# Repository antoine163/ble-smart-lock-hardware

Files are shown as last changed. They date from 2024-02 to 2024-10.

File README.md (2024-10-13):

# Bluetooth LE Smart Lock - Hardware

## Cartes électronique
Ce dépôt contient deux cartes :
- **[BleSmartLock](BleSmartLock/README.md)**: La carte principale, construite autour du bluenrg-m2, inclut toute l'électronique de contrôle pour la serrure.
- **[LightSensor](LightSensor/README.md)**: Cette carte contient le capteur de lumière, permettant de le placer à distance. Cette carte est optionnelle.

## Réalisation

### Liste du matérielle:
Cette liste de matériel est disponible sur Amazon.
- [Alimentation 12V](https://www.amazon.fr/dp/B0924XBMCF?ref=ppx_yo2ov_dt_b_fed_asin_title&th=1) pour alimenter la serrure.
- [Serrure électromécanique](https://www.amazon.fr/dp/B07KWMH16C?ref=ppx_yo2ov_dt_b_fed_asin_title) pour la partie électromécanique de la serrure.
- [Bouton lumineux](https://www.amazon.fr/dp/B0CBRFQLLT?ref=ppx_yo2ov_dt_b_fed_asin_title&th=1) pour l'ouverture de la serrure et visualisation de l'état de la serrure.
- [Boîtier étanche](https://www.amazon.fr/dp/B09V7M8759?ref=ppx_yo2ov_dt_b_fed_asin_title) pour recevoir la carte électronique principale *BleSmartLock*.
- [Câble 4 conducteurs](https://www.amazon.fr/dp/B0BFWJ19YJ?ref=ppx_yo2ov_dt_b_fed_asin_title&th=1) pour la connexion entre la carte électronique principale et:
    - La serrure électromécanique
    - Le bouton lumineux
    - L'éclairage d'ambiance
    - Le capteur de lumière
    - L'éclairage extérieur
- [Câble 2 conducteurs](https://www.amazon.fr/dp/B0B7WV1QCW?ref=ppx_yo2ov_dt_b_fed_asin_title) pour l'alimentation.
- [Presse-étoupes](https://www.amazon.fr/dp/B07V7F5HKQ?ref=ppx_yo2ov_dt_b_fed_asin_title&th=1) pour faire passer les différents câbles dans les boîtiers étanches.
- [Boîtier étanche](https://www.amazon.fr/dp/B0BZCS1PN1?ref=ppx_yo2ov_dt_b_fed_asin_title) pour recevoir le capteur de luminosité *LightSensor* et la lampe extérieur *Mini-Light*.
- [Colle epoxy transparent](https://www.amazon.fr/dp/B07JL8JC3N?ref=ppx_yo2ov_dt_b_fed_asin_title) pour réaliser une vitre dans le boîtier du capteur de luminosité et de la lampe extérieur.

### Mise en boiter de la carte principal *BleSmartLock* 
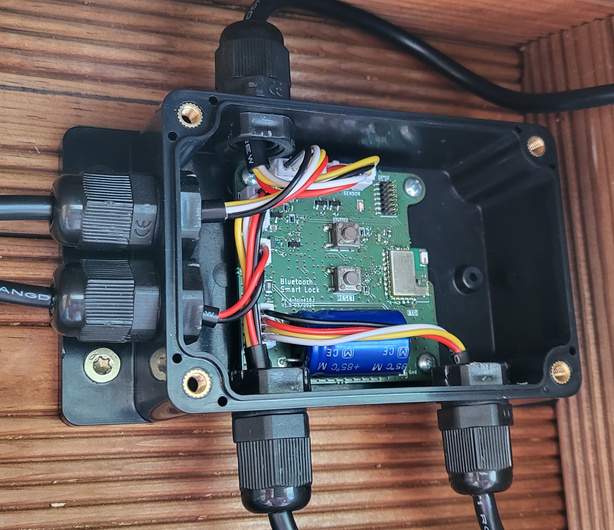
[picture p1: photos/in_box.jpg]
in box
  

### Mise en boiter de la carte capteur *LightSensor* et lampe extérieur *Mini-Light*
On notera ici que 2 cartes *Mini-Light* ont été utilisées pour augmenter la luminosité de la lampe extérieur.  
**NOTE:** Un maximum de 2 cartes *Mini-Light* peut être utilisé directement à la carte principale *BleSmartLock*.  
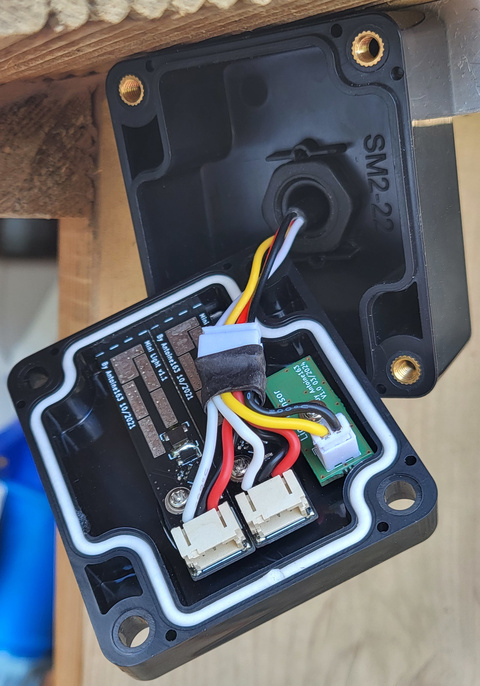
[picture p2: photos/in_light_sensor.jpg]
in light sensor


Au préalable, il est nécessaire de percer un trou rectangulaire et un trou rond dans le couvercle du boîtier, puis de les remplir de colle époxy transparente. Cela permet de créer des vitres, assurant ainsi le passage de la lumière utile au capteur de luminosité et d'éclairage extérieur.  
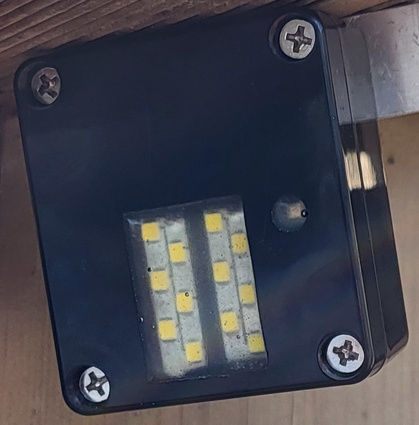
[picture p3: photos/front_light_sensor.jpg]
front light sensor


## Prototypes
### Avec les cartes v1.0
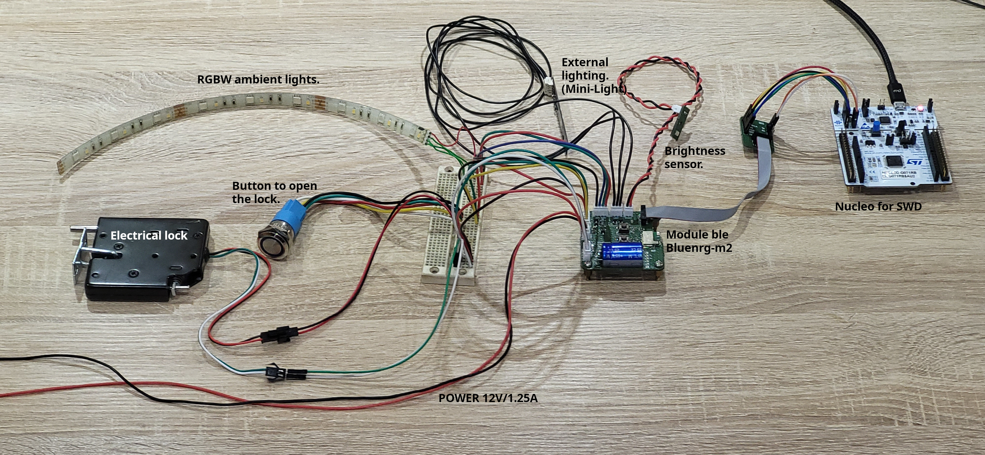
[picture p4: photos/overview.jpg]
Prototype cartes v1.0


### Sur plaque d'essai
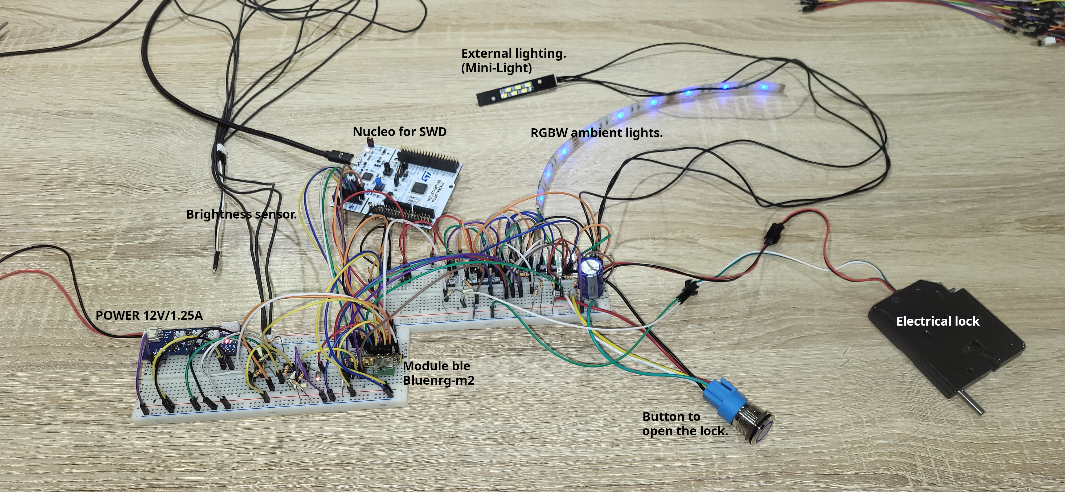
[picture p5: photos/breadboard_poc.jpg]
Prototype breadboard


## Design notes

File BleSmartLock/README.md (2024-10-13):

# BleSmartLock Board
Cette carte est la carte principale du projet. Elle est basée sur le module radio Bluenrg-m2 et fais l'interface avec les autres organes, telle que la serrure elle-même et le bouton pour l'ouverture.

Voir le [README](../../Firmware/README.md) du firmware pour la programmation de cette carte.

## Vue 3D
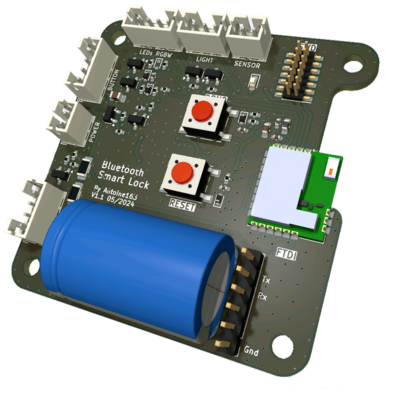
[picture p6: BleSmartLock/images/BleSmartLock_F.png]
BleSmartLock front
 
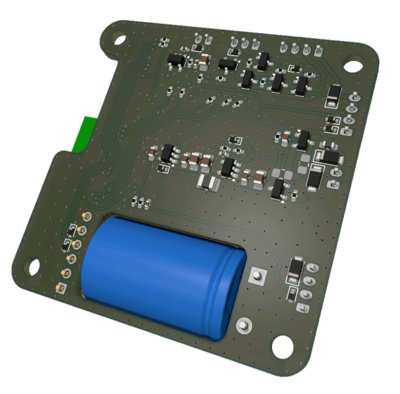
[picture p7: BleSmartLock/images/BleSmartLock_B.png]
BleSmartLock back
 

## Réalisation
### Fabrication de la version v1.0
#### Correction
Une erreur c'est glissée à la saisie de la schématique. DIO12 peut seulement être une entrée. la version v1.1 inverse DIO12 avec DIO6.
Il faut inverser c'est deux gpio sur le pcb en coupent deux pistes et en croisent les connections.
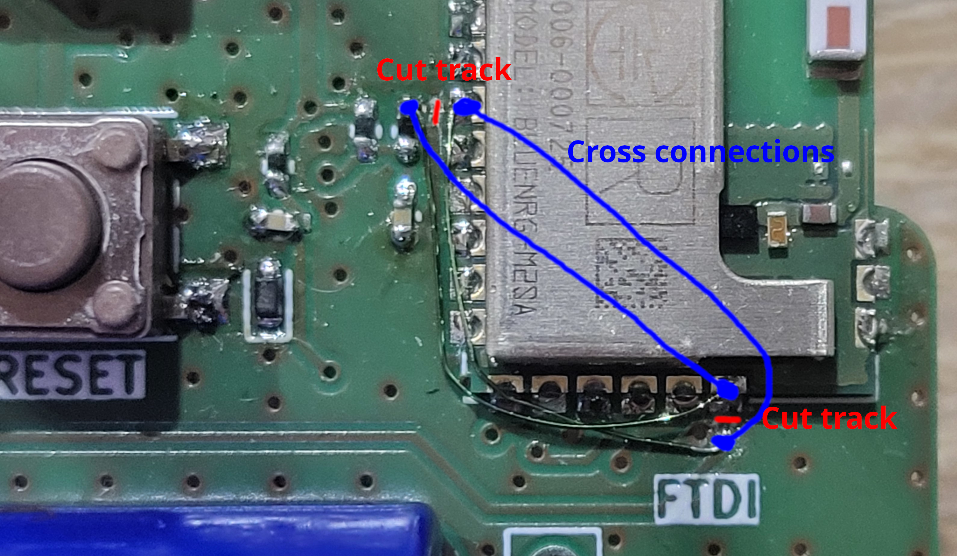
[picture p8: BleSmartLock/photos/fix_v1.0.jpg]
BleSmartLock fix v1.0


#### Photos
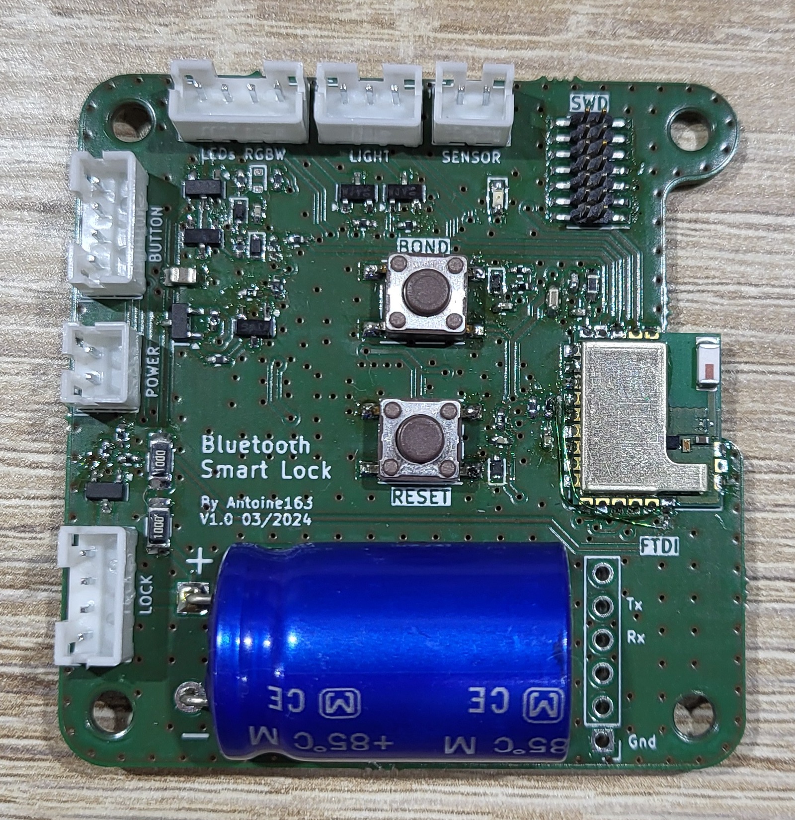
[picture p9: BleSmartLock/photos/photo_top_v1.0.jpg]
BleSmartLock photo top

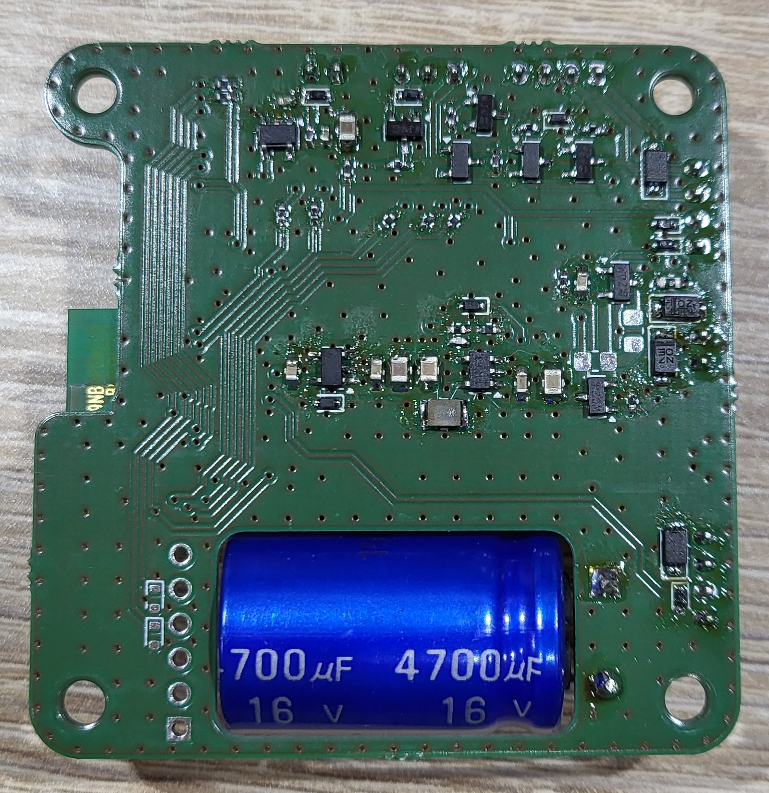
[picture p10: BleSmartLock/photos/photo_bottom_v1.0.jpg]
BleSmartLock photo top

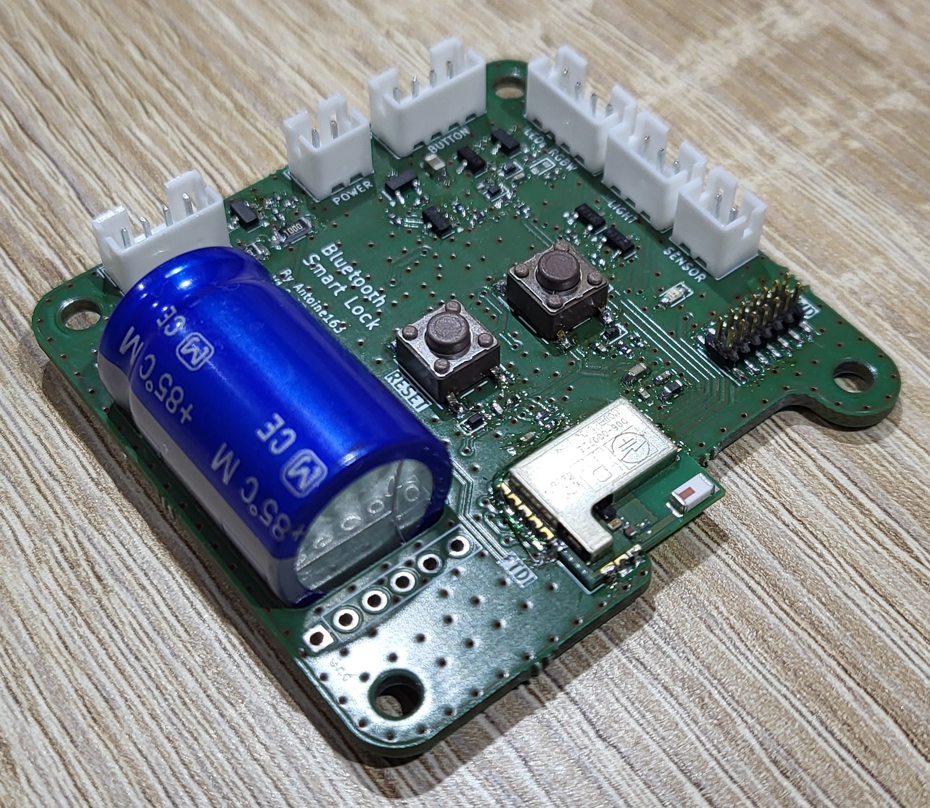
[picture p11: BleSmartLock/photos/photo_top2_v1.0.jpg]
BleSmartLock photo top

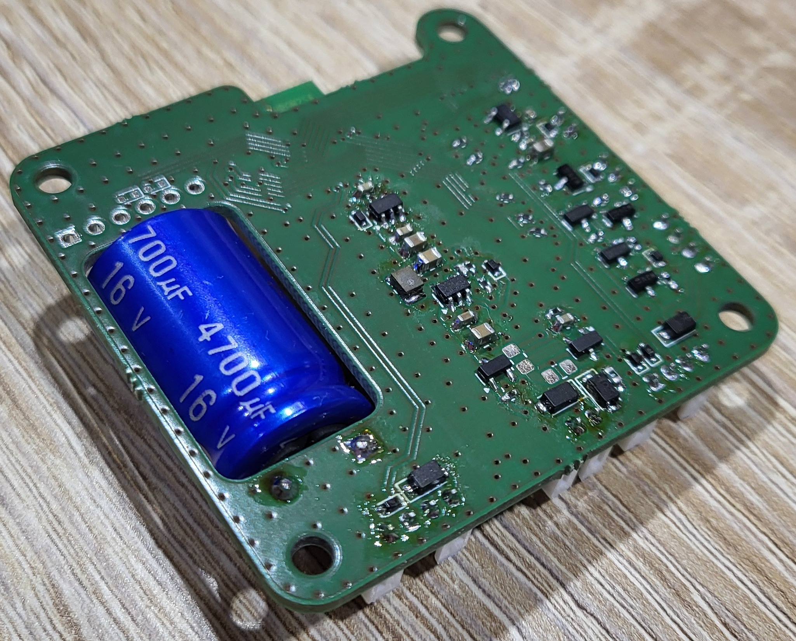
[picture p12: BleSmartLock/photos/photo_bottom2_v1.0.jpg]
BleSmartLock photo top


#### BOM
La bom interactive est trouvable [ici](https://antoine163.github.io/ble-smart-lock-hardware/Ble_Smart_Lock_1.0-ibom.html). 

### Fabrication de la version v1.1
Je n'est pas fabrique cette version, mais elle dispose exactement des mêmes composent que la v1.0.
La bom interactive est trouvable [ici](https://antoine163.github.io/ble-smart-lock-hardware/Ble%20Smart%20Lock-1.1-ibom.html). 

# Schématique





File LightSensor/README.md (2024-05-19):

# BleSmartLock-LightSensor Board
C'est la carte satellite permettant de déporter le capteur de luminosité. Elle est constituée principalement du capteur KPS-3227.

## Vue 3D
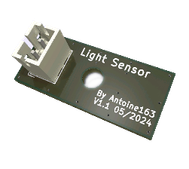
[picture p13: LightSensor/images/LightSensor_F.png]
LightSensor front
 
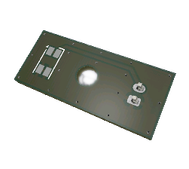
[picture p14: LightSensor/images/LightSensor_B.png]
LightSensor back
 

## Réalisation
### Fabrication de la version v1.0
#### Photos
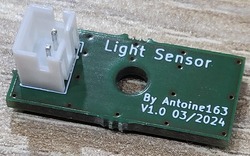
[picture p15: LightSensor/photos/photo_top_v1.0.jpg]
BleSmartLock photo top

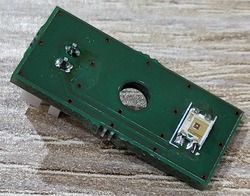
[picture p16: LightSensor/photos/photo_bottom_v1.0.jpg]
BleSmartLock photo bottom


#### BOM
Cette carte est constituée seulement d'un connecteur JST et du capteur de lumière ambiante:
- JST: [B2B-PH-K-S](https://www.amazon.fr/gp/product/B0731MZCGF/ref=ppx_yo_dt_b_asin_title_o02_s00?ie=UTF8&psc=1).
- KINGBRIGHT: [KPS-3227SP1C](https://fr.farnell.com/kingbright/kps-3227sp1c/capteur-optique-phototransistor/dp/2373478). 

### Fabrication de la version v1.1
Je n'est pas fabrique cette version, seulement le connecteur à été tournée de 180 degrés.

# Schématique


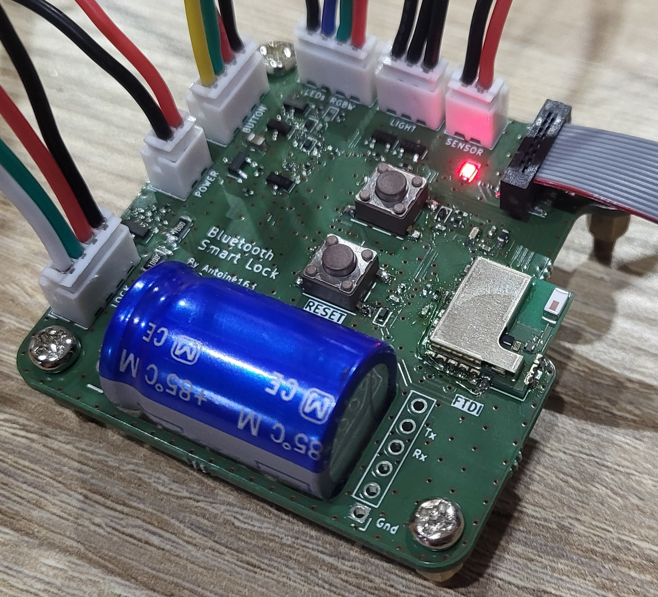
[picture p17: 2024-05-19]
BleSmartLock/photos/photo_top_v1.0back.jpg

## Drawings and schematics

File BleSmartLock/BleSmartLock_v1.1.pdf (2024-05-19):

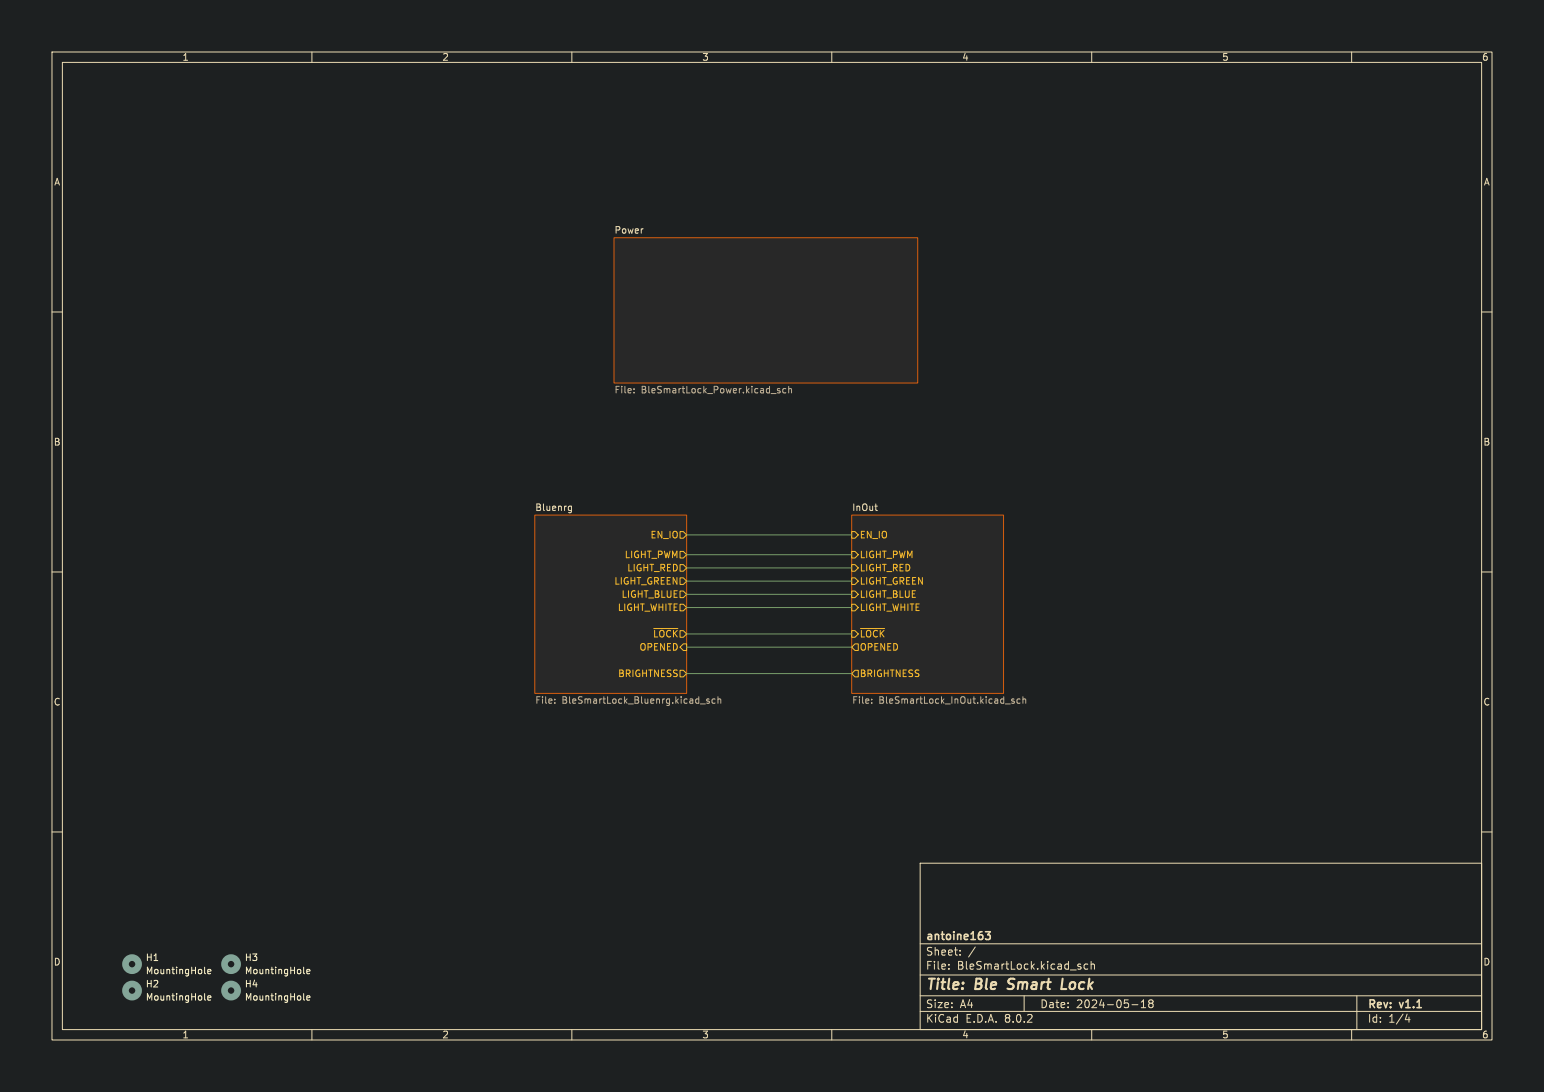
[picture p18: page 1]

Id: 1/4 Title: Ble Smart Lock

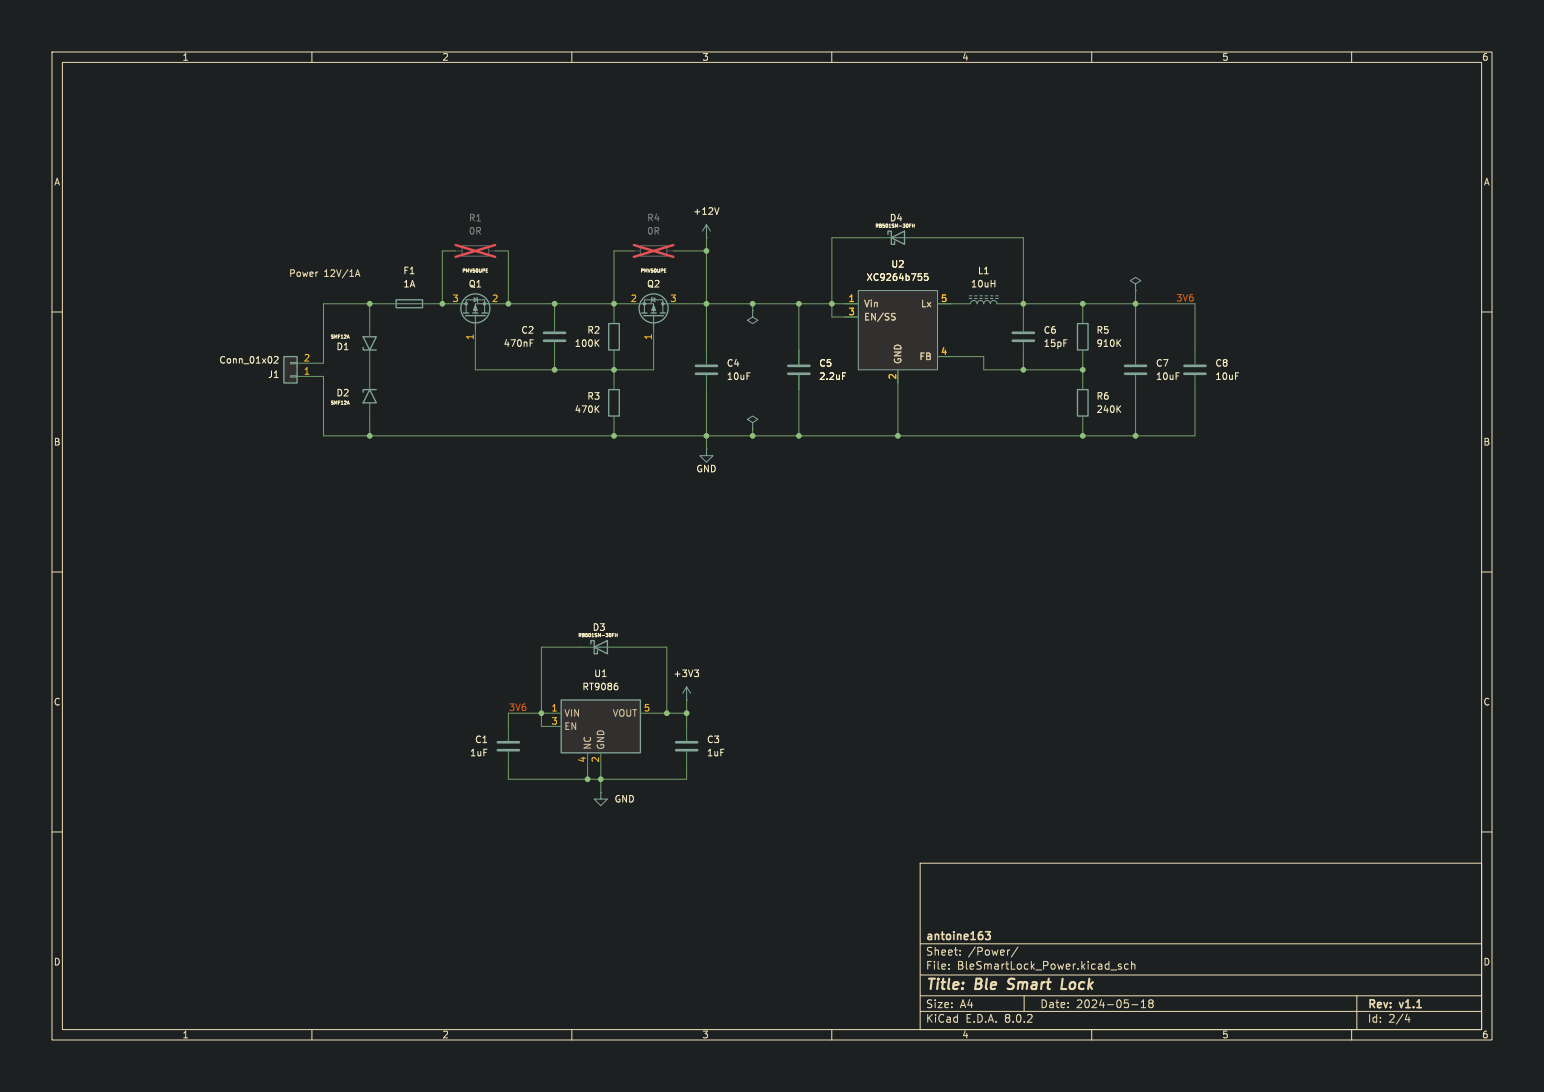
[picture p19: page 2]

Id: 2/4 Title: Ble Smart Lock

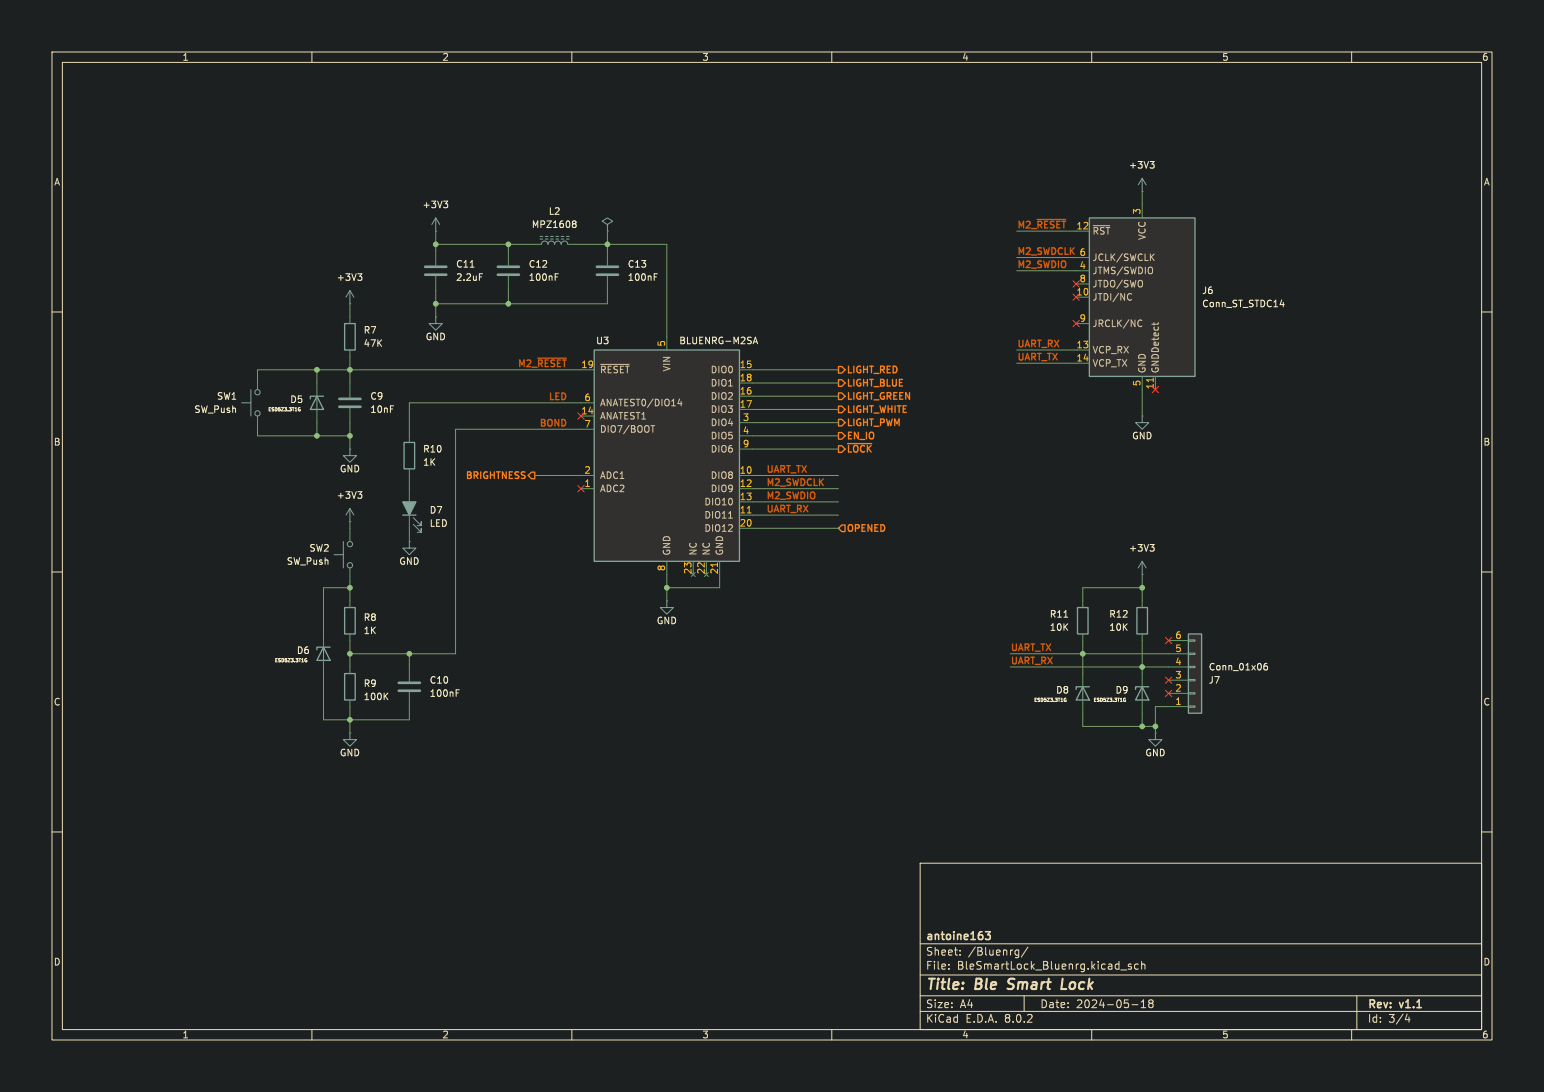
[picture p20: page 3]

Id: 3/4 Title: Ble Smart Lock

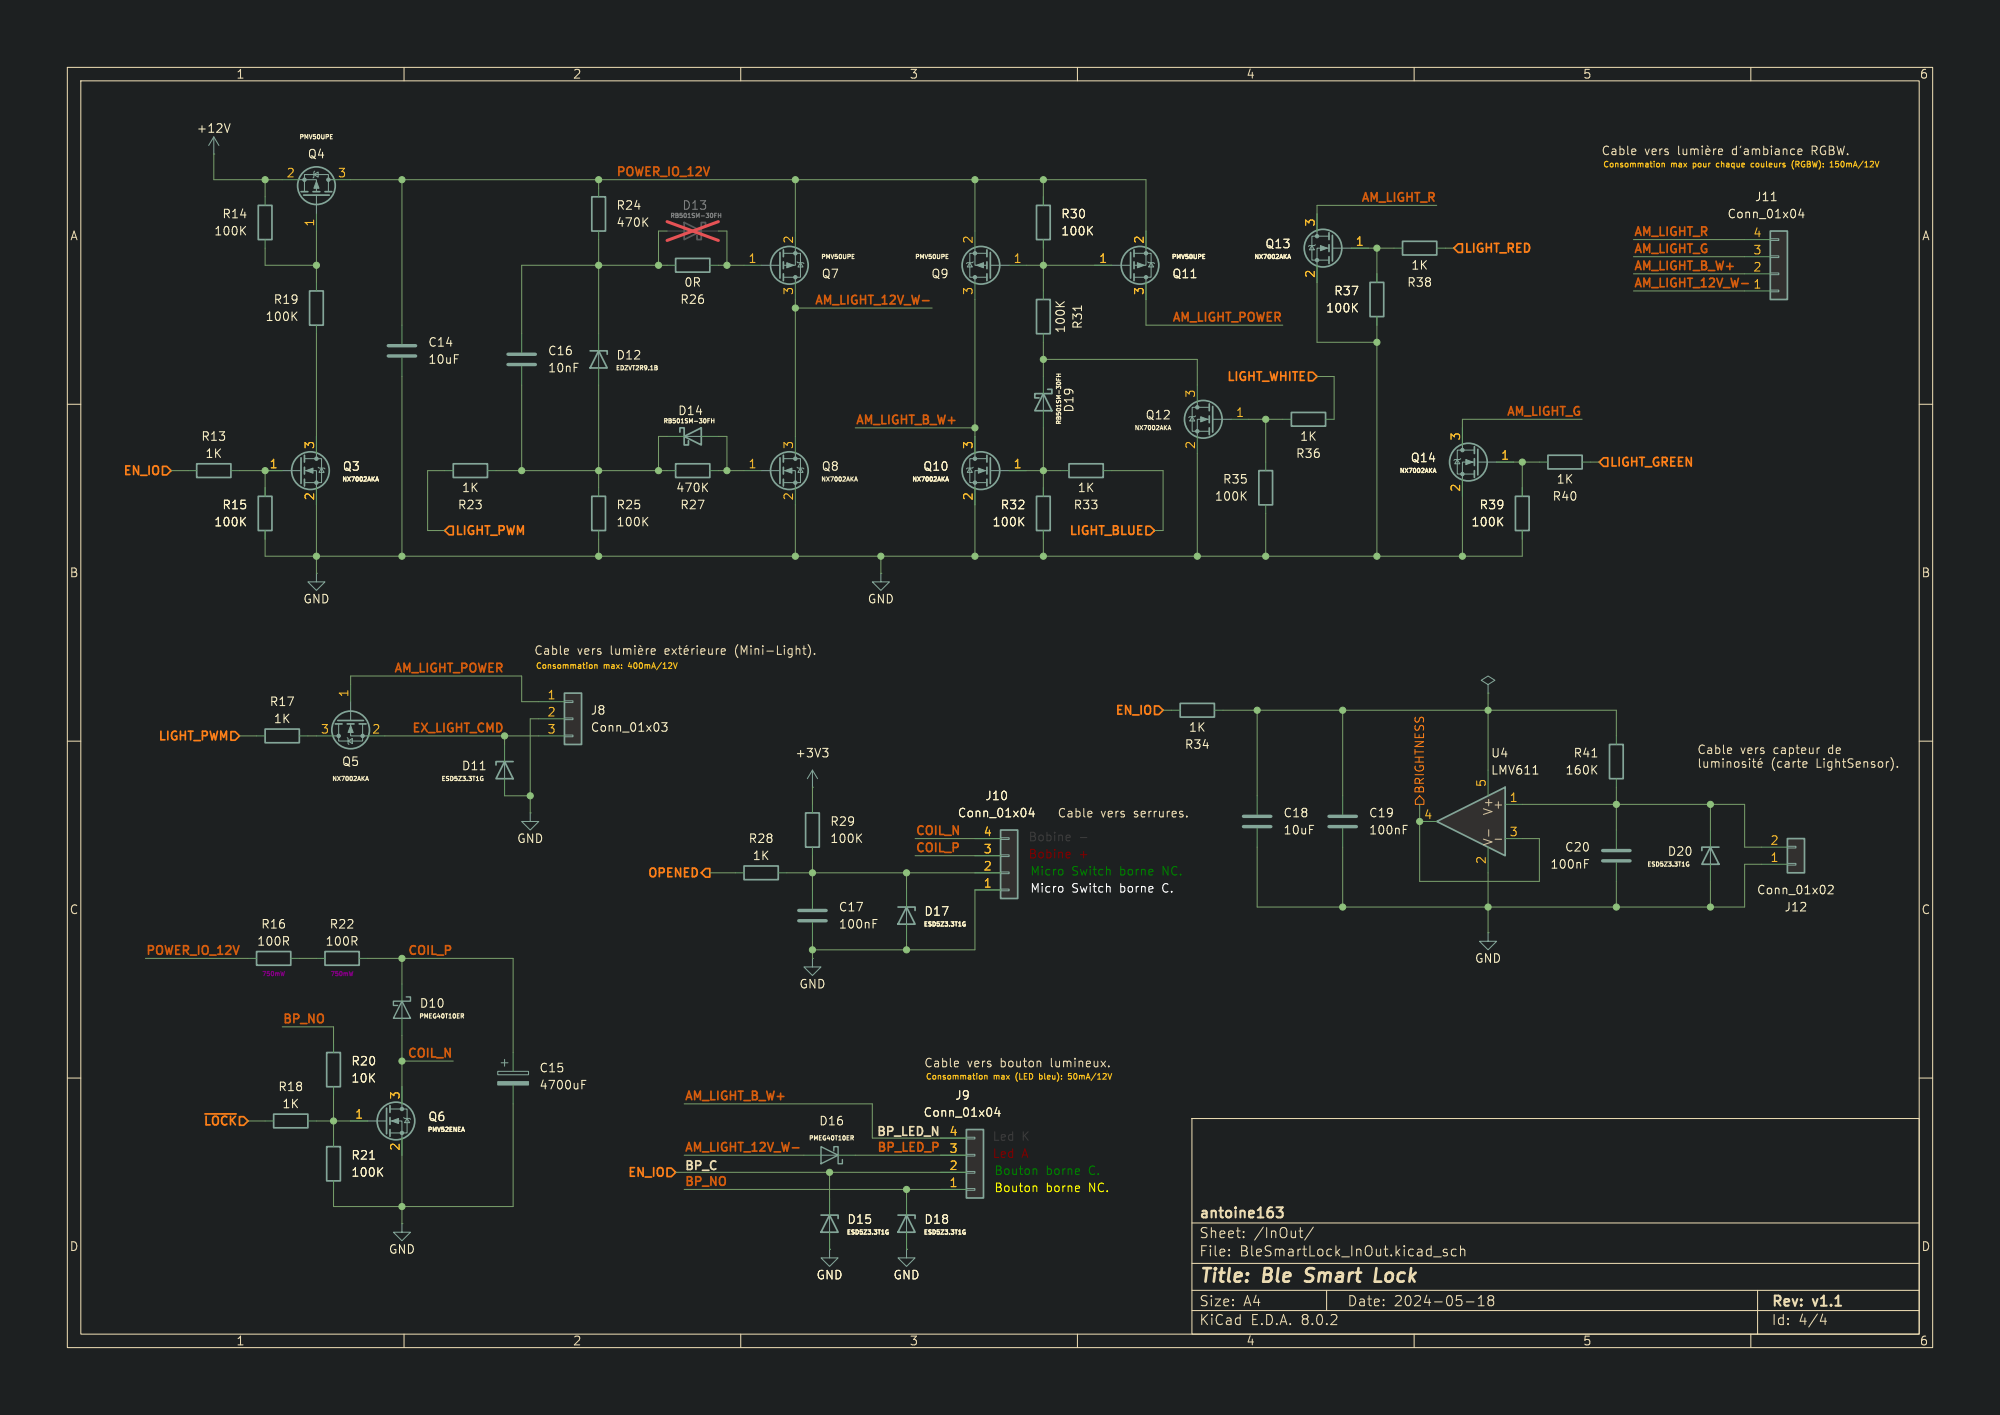
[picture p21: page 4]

þÿluminosité (carte LightSensor). Bobine - Cable vers bouton lumineux.

Id: 4/4 Title: Ble Smart Lock

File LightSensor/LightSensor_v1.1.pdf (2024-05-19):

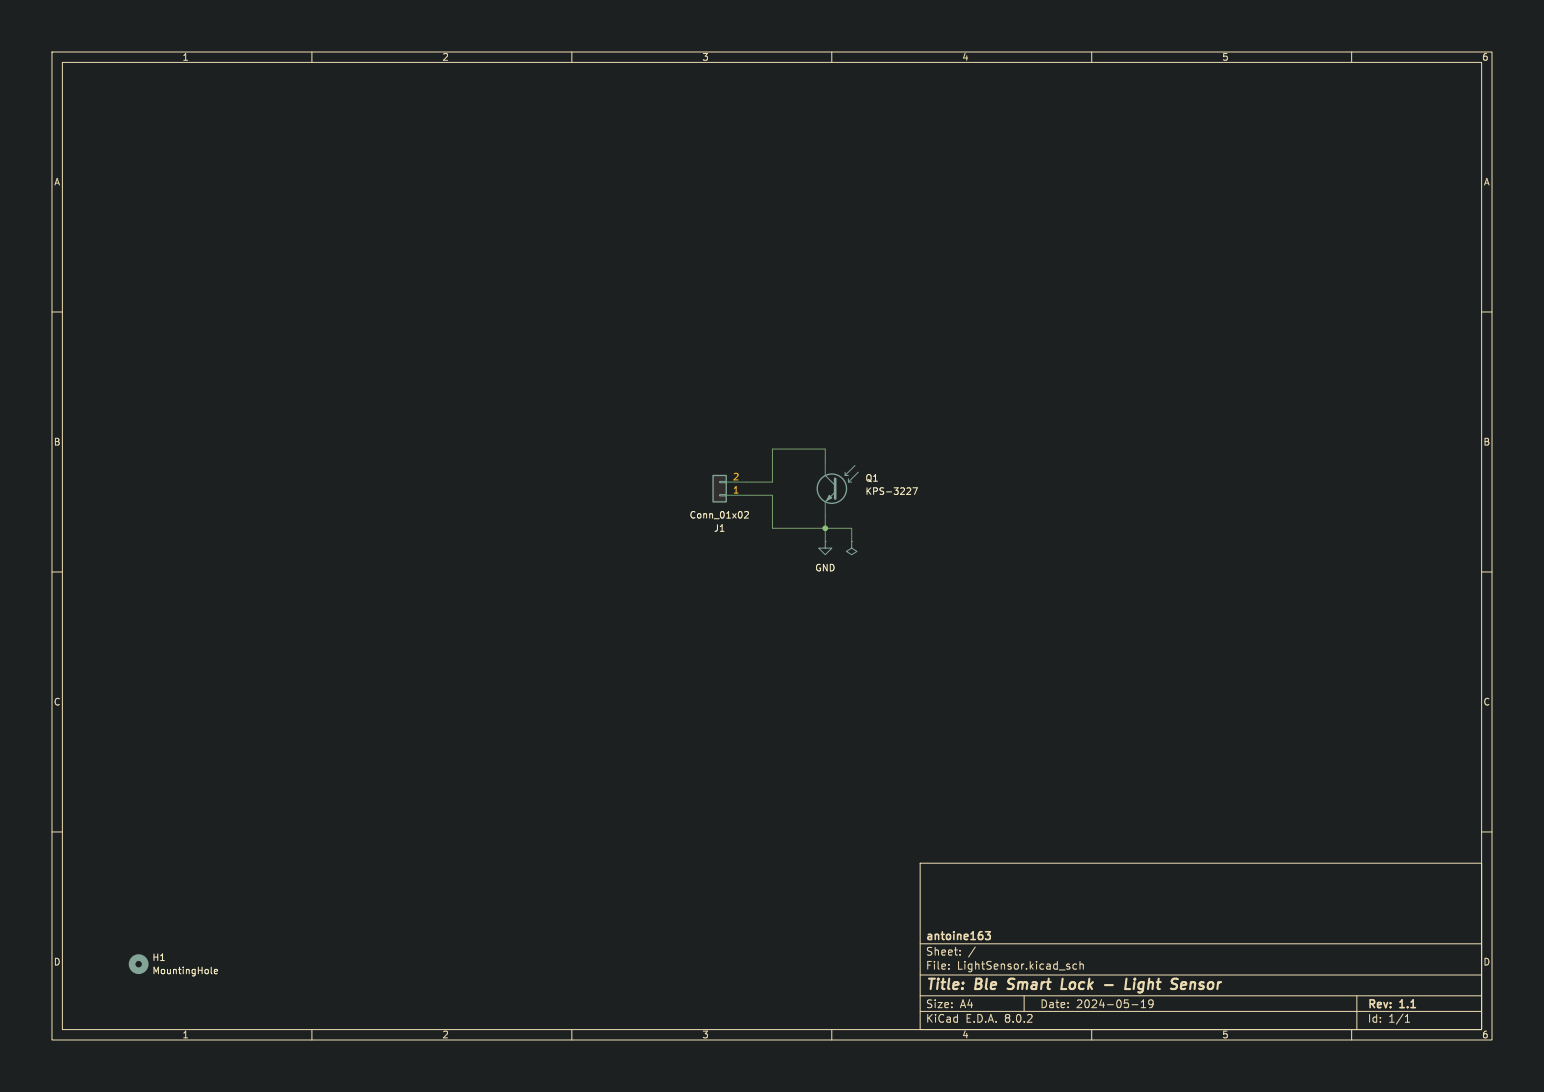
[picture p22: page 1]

Id: 1/1 Title: Ble Smart Lock - Light Sensor File: LightSensor.kicad_sch Sheet: / antoine163 H1 MountingHole

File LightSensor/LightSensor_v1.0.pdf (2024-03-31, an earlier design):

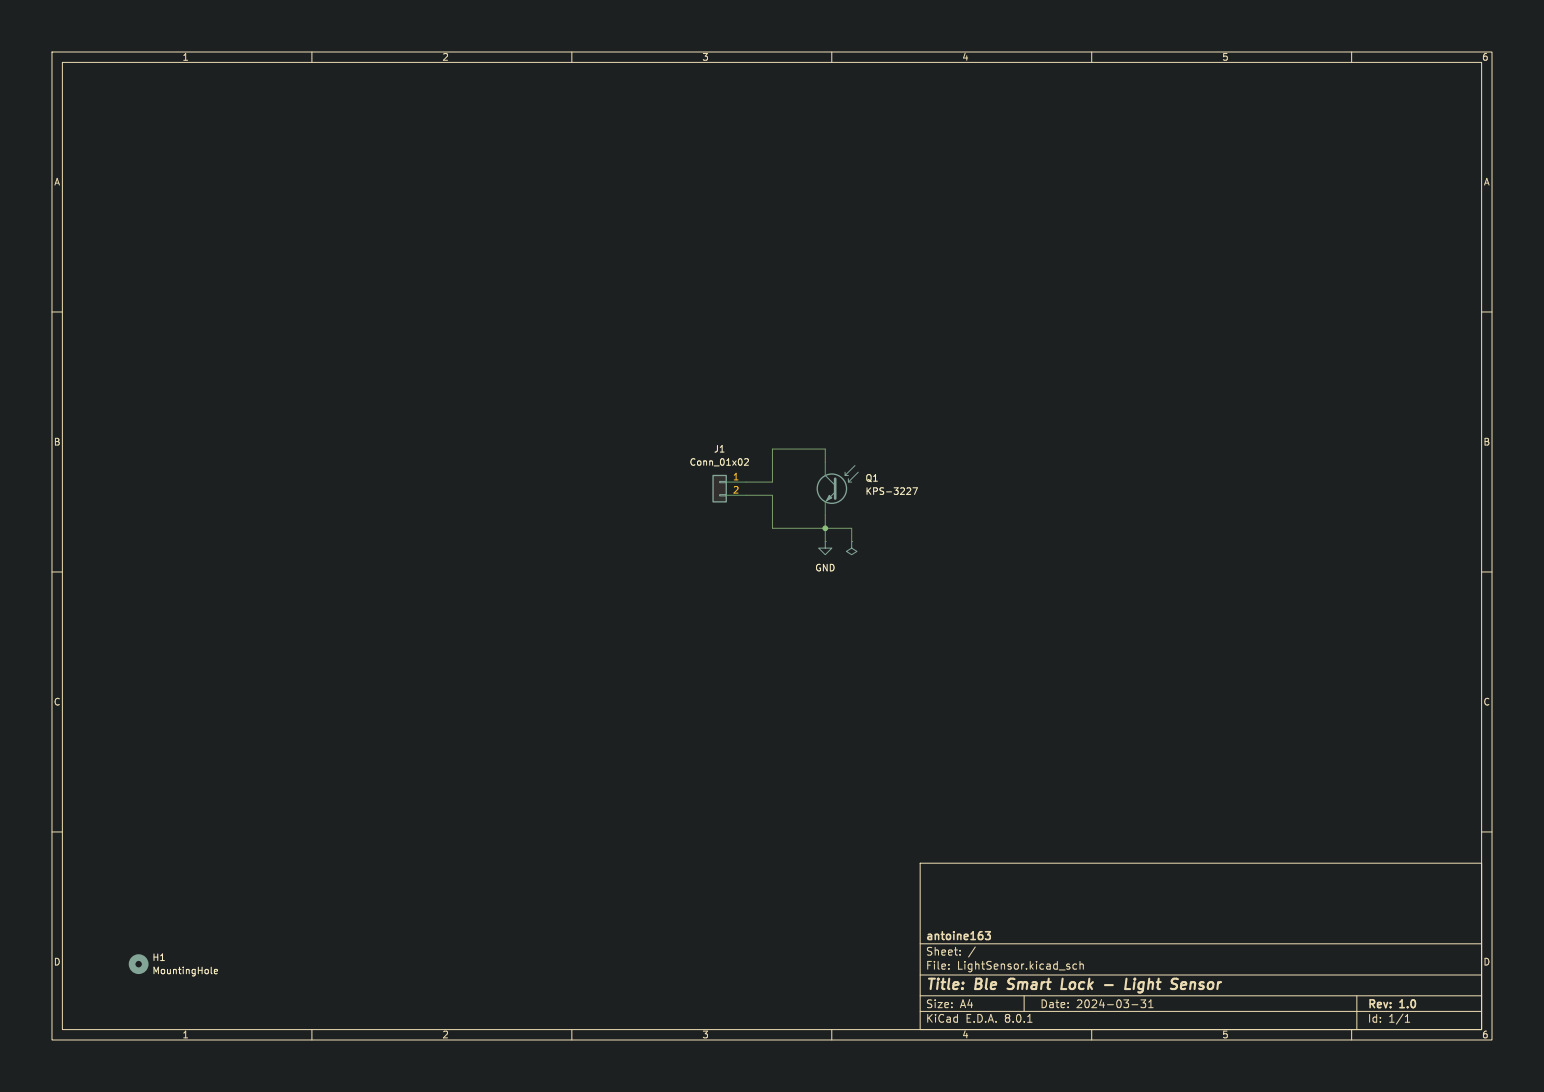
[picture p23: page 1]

Id: 1/1 Title: Ble Smart Lock - Light Sensor File: LightSensor.kicad_sch Sheet: / antoine163 H1 MountingHole

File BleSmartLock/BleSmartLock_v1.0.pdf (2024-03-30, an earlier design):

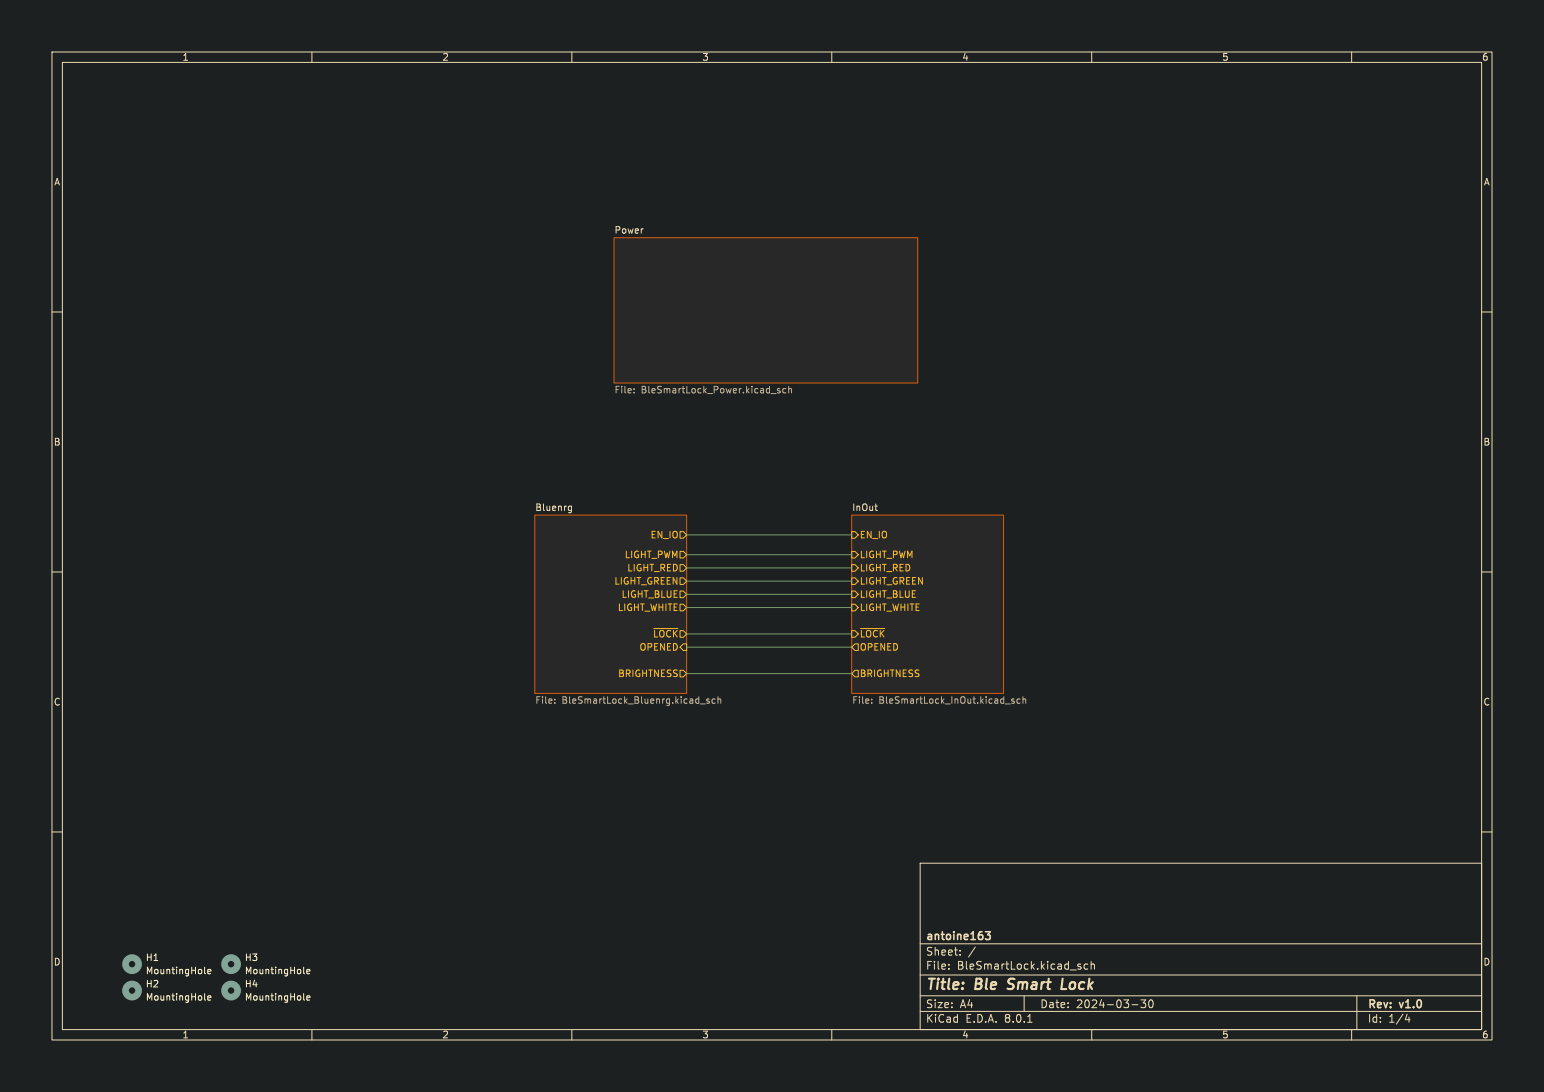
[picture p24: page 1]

Id: 1/4 Title: Ble Smart Lock

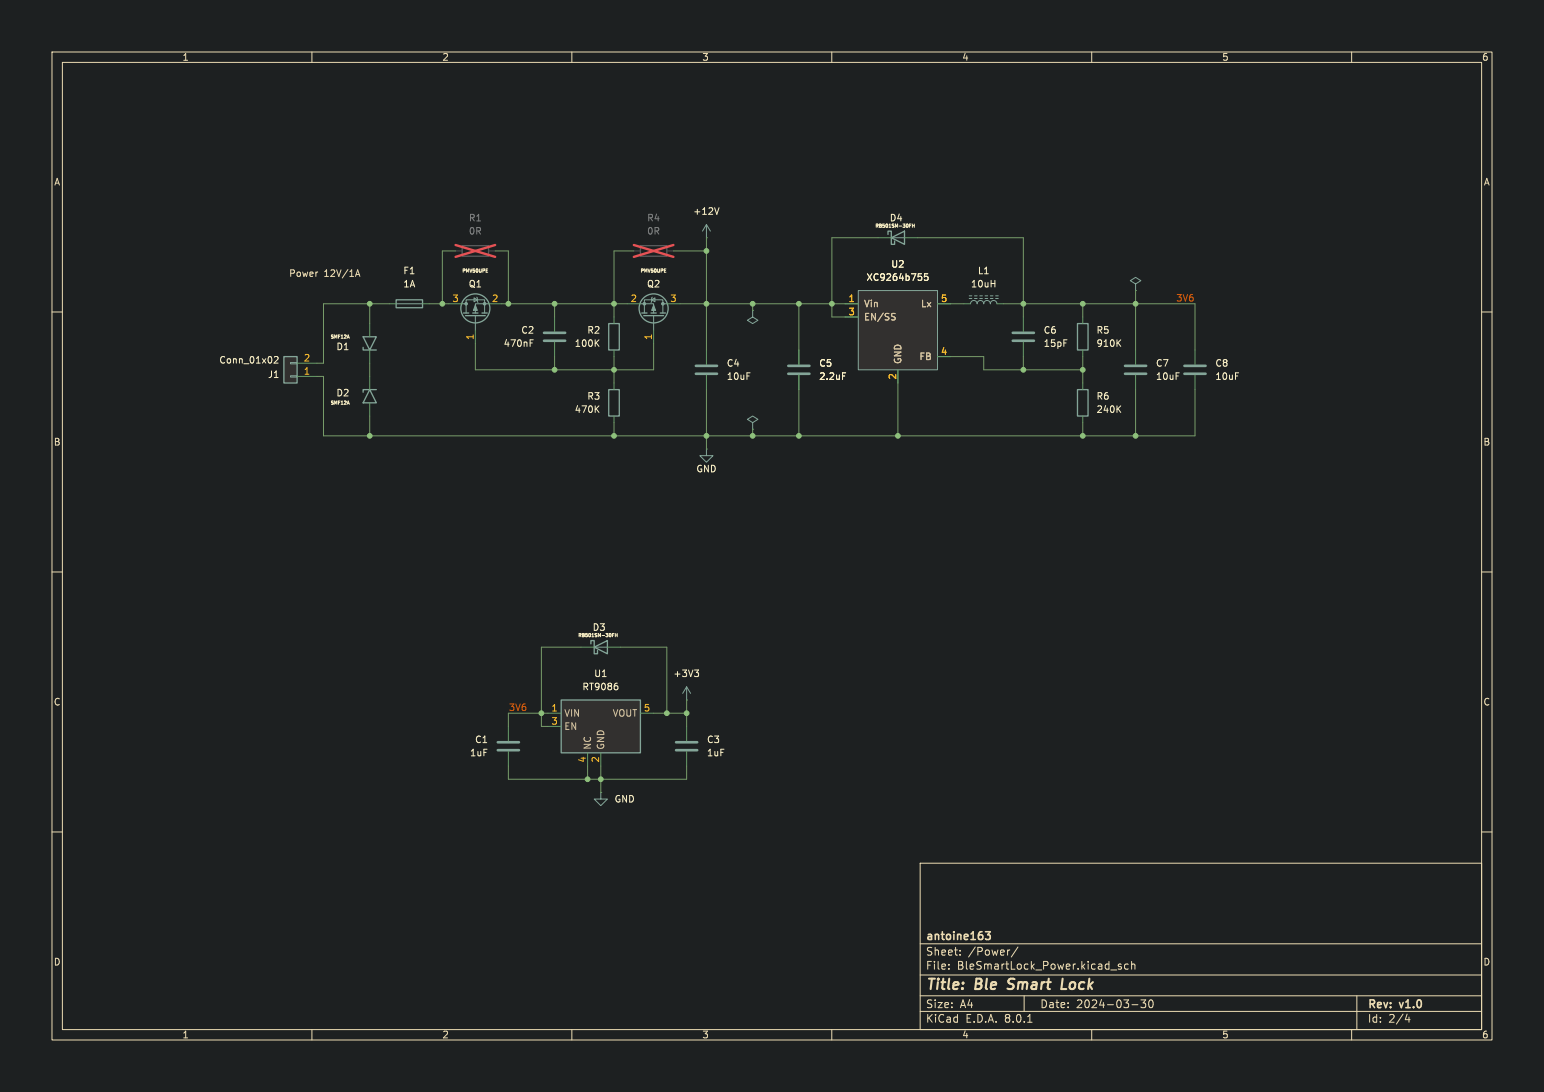
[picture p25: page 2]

Id: 2/4 Title: Ble Smart Lock

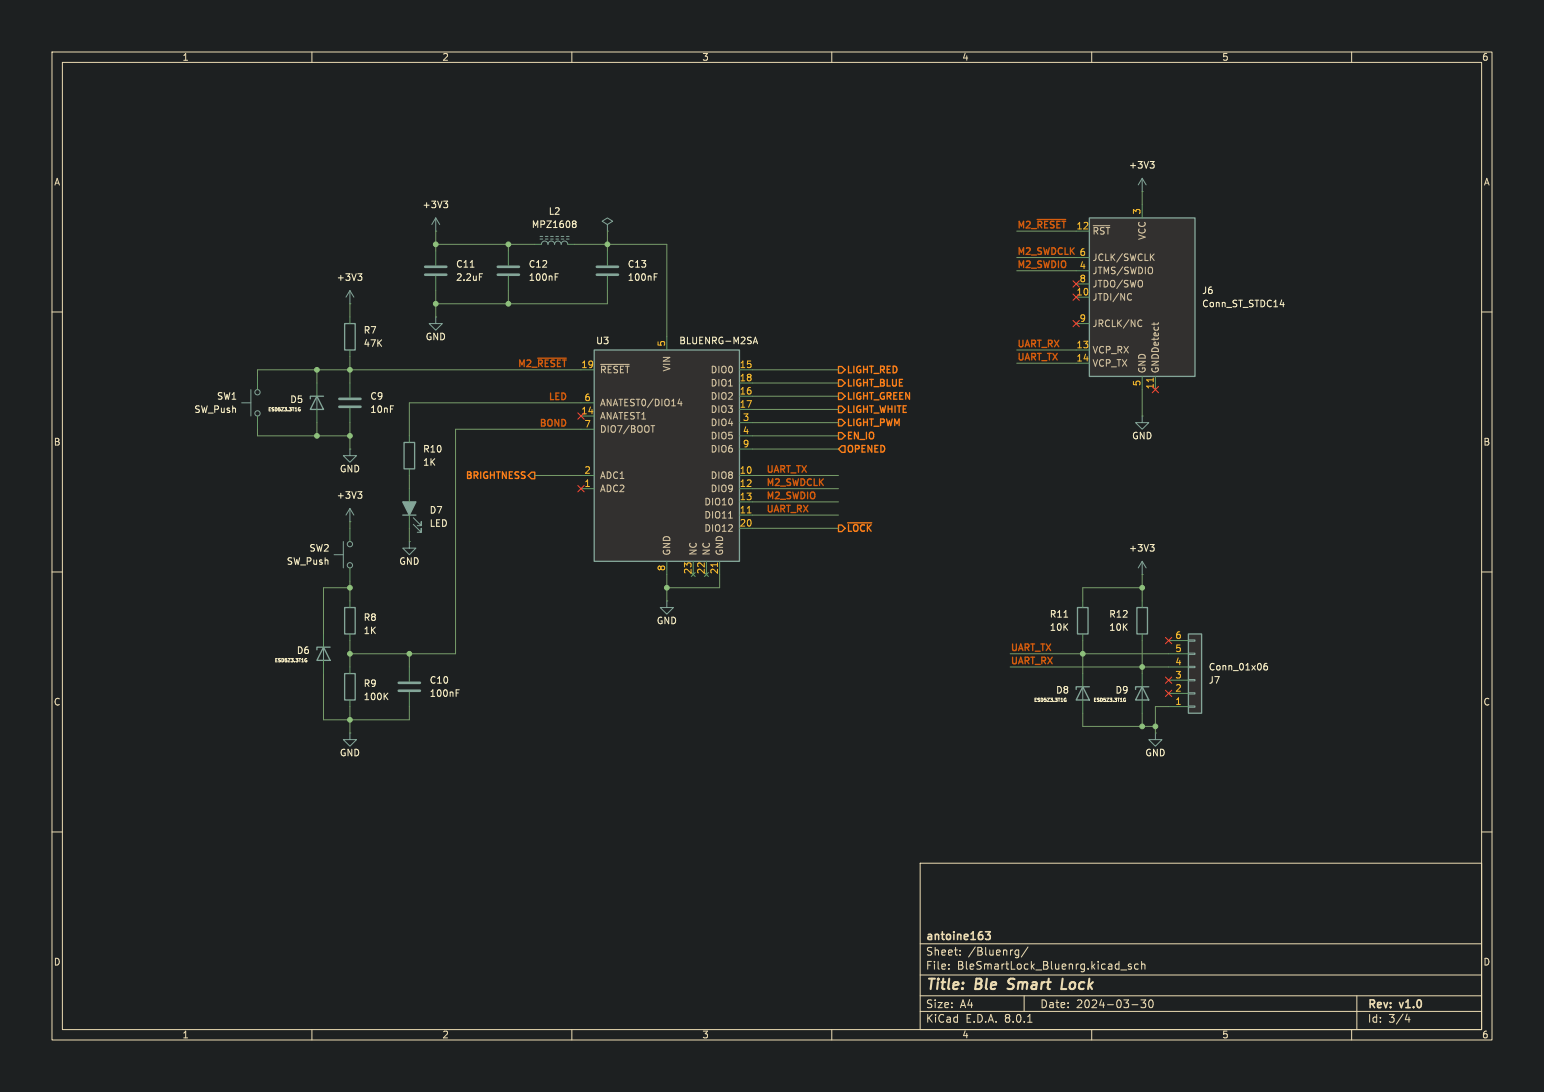
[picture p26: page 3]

Id: 3/4 Title: Ble Smart Lock

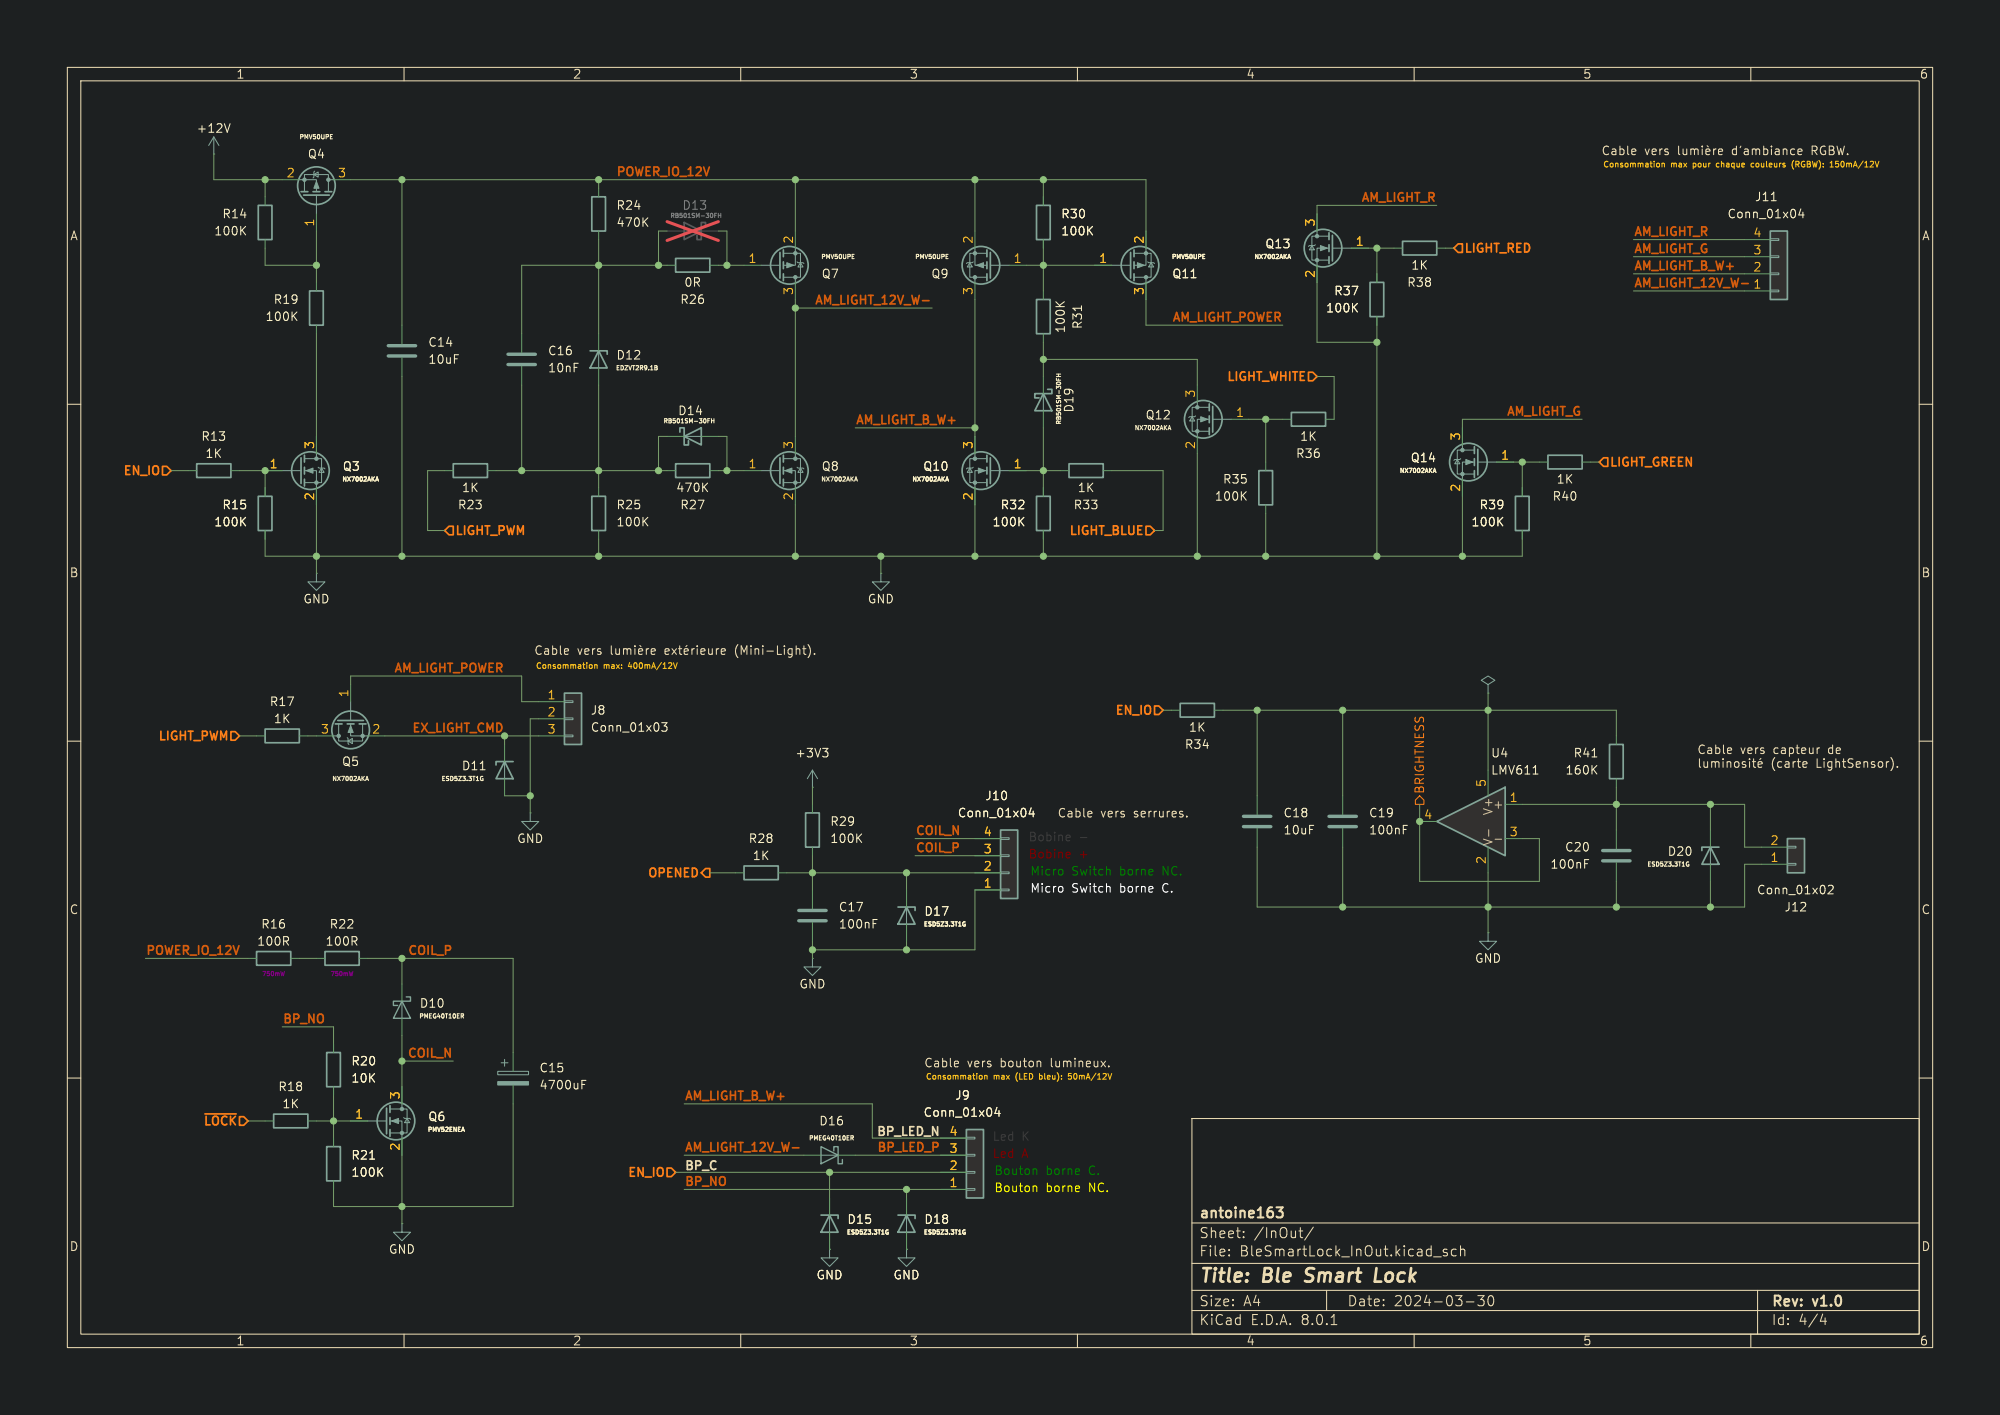
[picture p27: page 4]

þÿluminosité (carte LightSensor). Bobine - Cable vers bouton lumineux.

Id: 4/4 Title: Ble Smart Lock

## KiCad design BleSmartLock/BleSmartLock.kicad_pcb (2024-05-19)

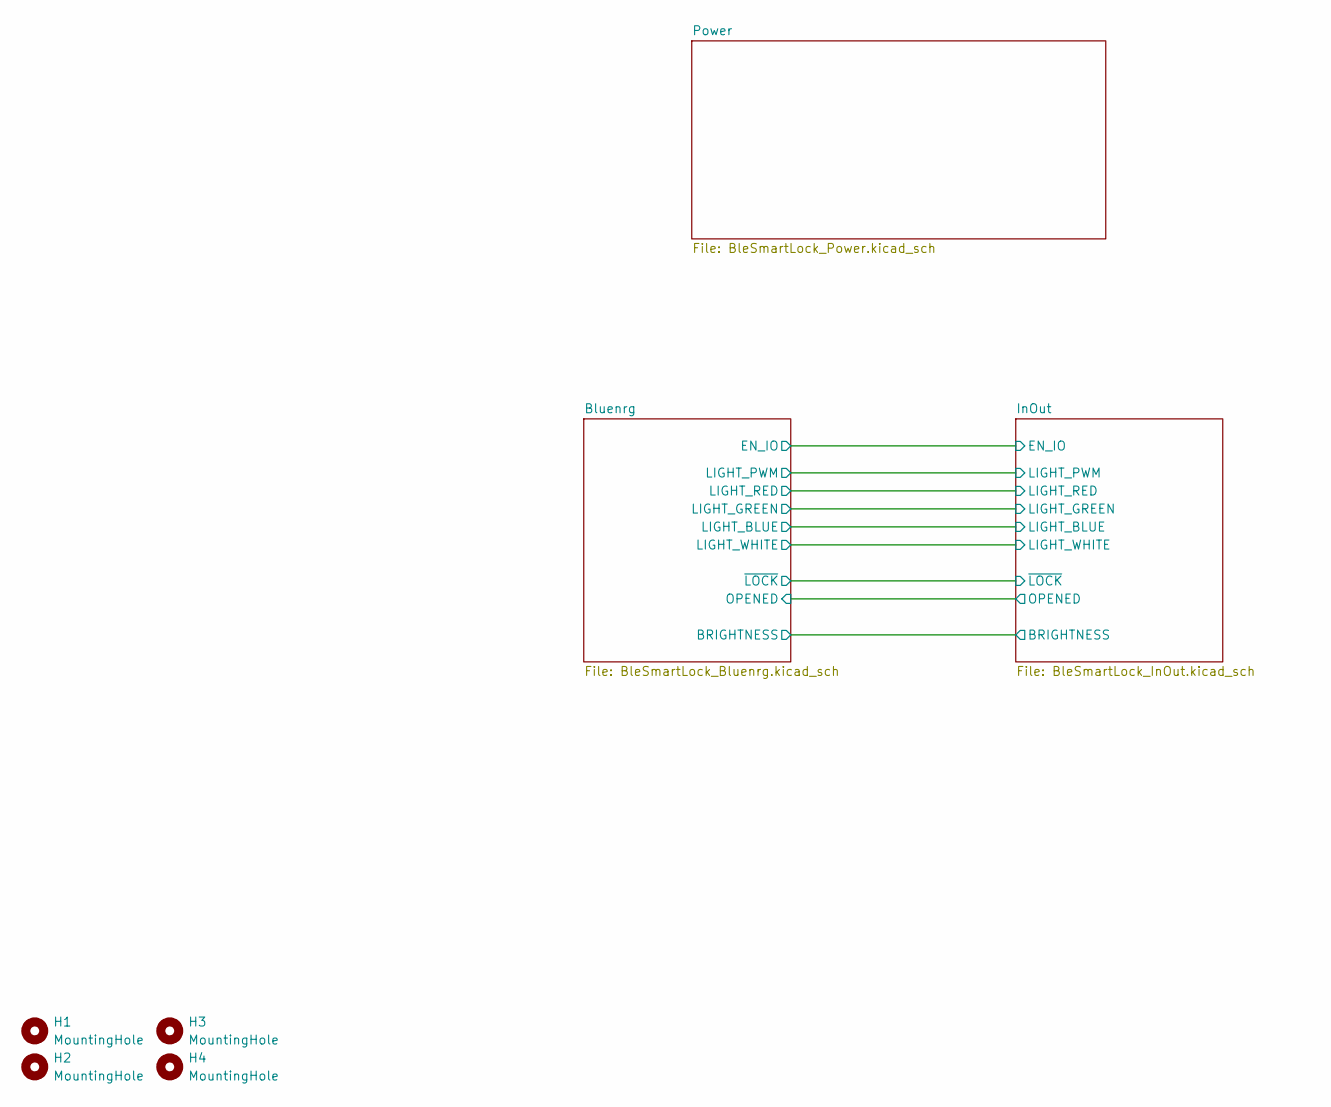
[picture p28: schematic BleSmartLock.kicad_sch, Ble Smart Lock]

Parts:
H1, H2, H3, H4: MountingHole; MountingHole_3.2mm_M3

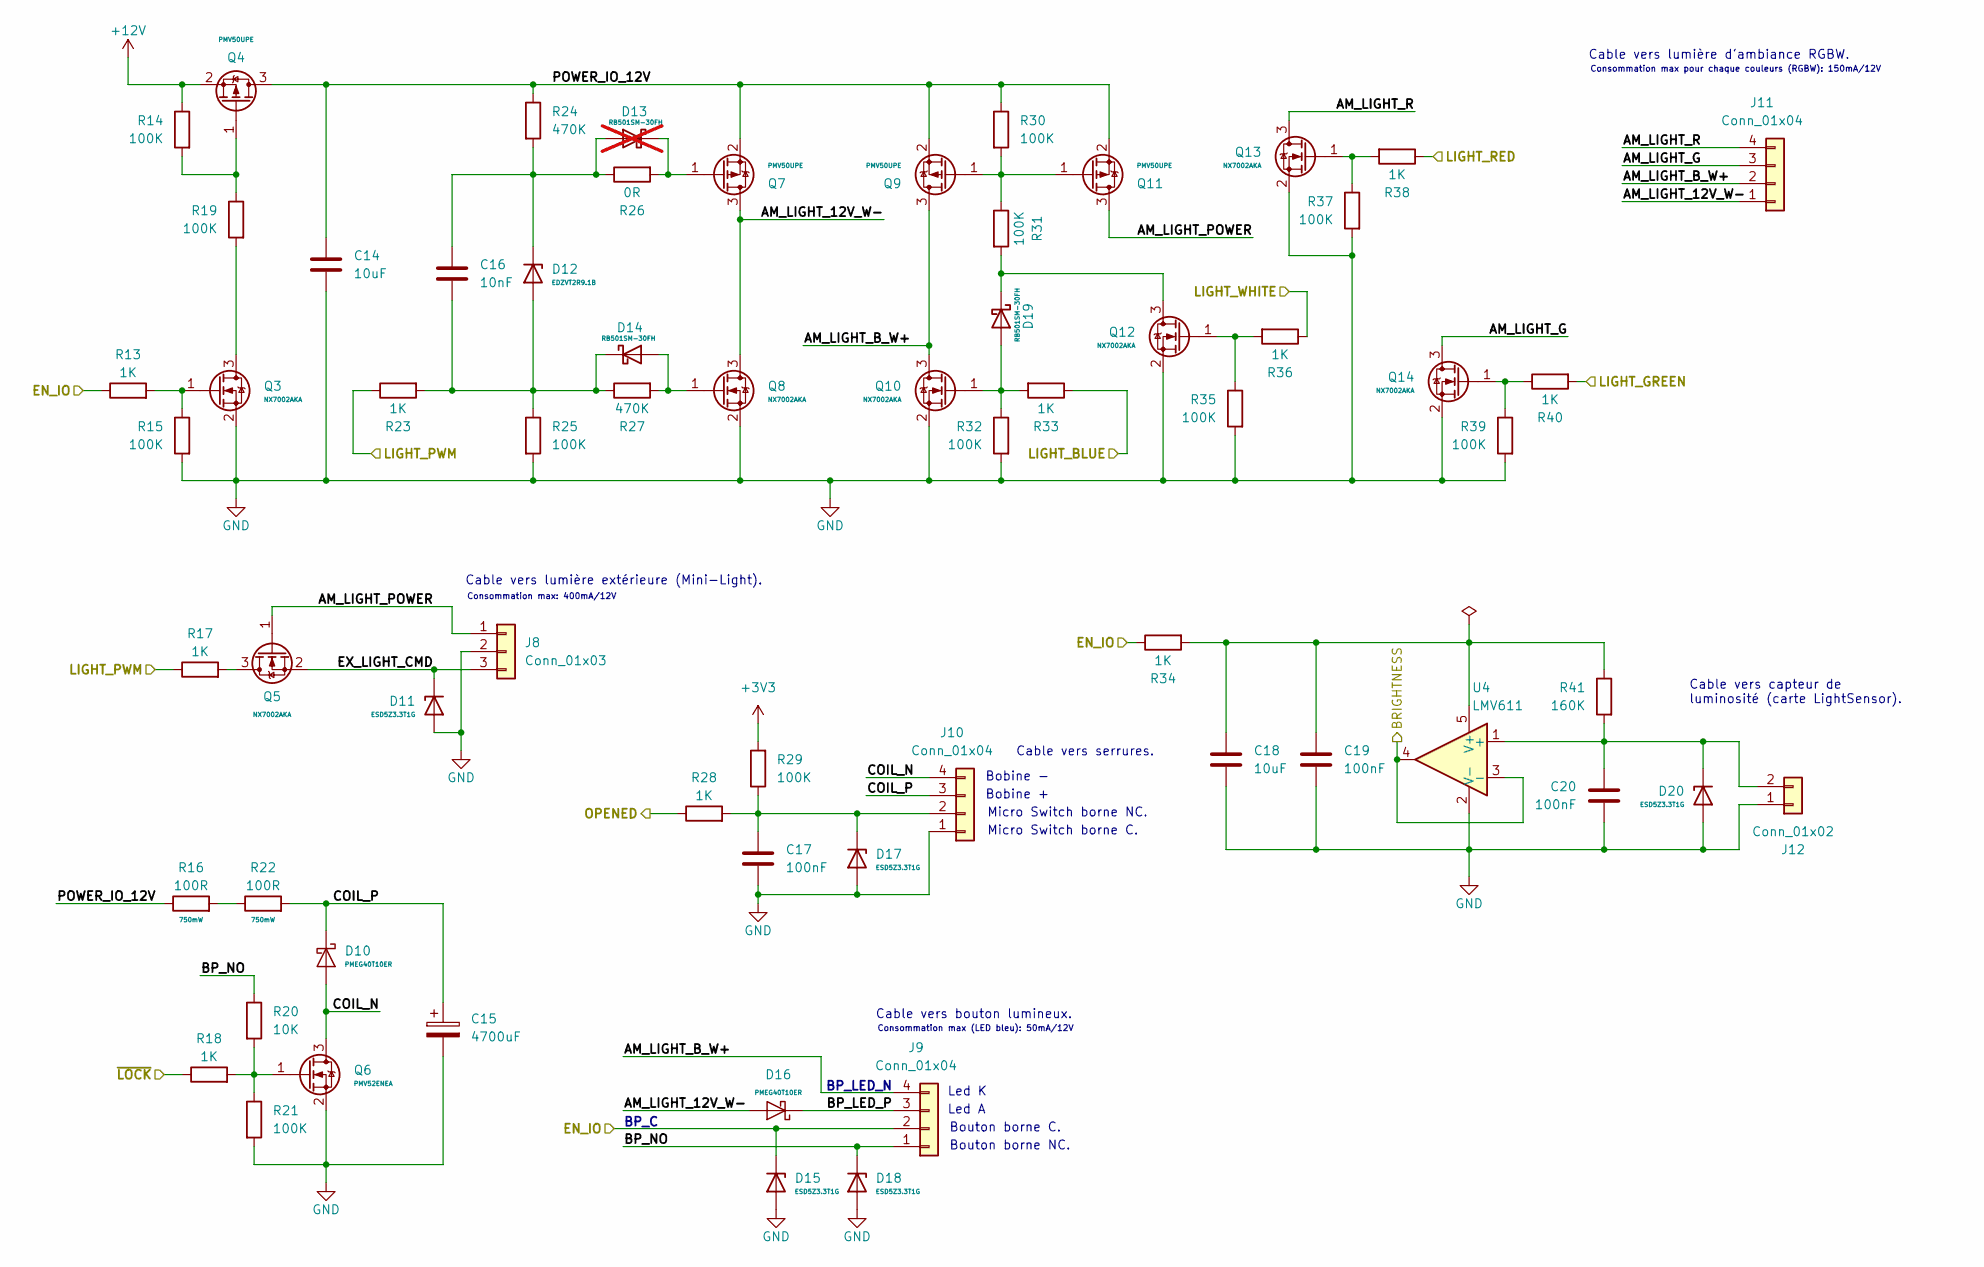
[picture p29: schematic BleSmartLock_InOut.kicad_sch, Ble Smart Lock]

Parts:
C14, C18: 10uF; C_0805_2012Metric_Pad1.18x1.45mm_HandSolder
C15: 4700uF; CP_Radial_L25.0mm_D16.0mm_P7.50mm_Horizontal_EdgeCuts
C16: 10nF; C_0402_1005Metric_Pad0.74x0.62mm_HandSolder
C17, C19, C20: 100nF; C_0402_1005Metric_Pad0.74x0.62mm_HandSolder
D10, D16: PMEG40T10ER; Nexperia_CFP3_SOD-123W
D11, D15, D17, D18, D20: ESD5Z3.3T1G; D_SOD-523
D12: EDZVT2R9.1B; D_SOD-523
D13: RB501SM-30FH; D_SOD-523; not fitted
D14, D19: RB501SM-30FH; D_SOD-523
J8: Conn_01x03; JST_PH_B3B-PH-K_1x03_P2.00mm_Vertical
J9, J10, J11: Conn_01x04; JST_PH_B4B-PH-K_1x04_P2.00mm_Vertical
J12: Conn_01x02; JST_PH_B2B-PH-K_1x02_P2.00mm_Vertical
Q3, Q5, Q8, Q10, Q12, Q13, Q14: NX7002AKA; SOT-23
Q4, Q7, Q9, Q11: PMV50UPE; SOT-23
Q6: PMV52ENEA; SOT-23
R13, R17, R18, R23, R28, R33, R34, R36, R38, R40: 1K; R_0402_1005Metric_Pad0.72x0.64mm_HandSolder
R14, R15, R19, R21, R25, R29, R30, R31, R32, R35, R37, R39: 100K; R_0402_1005Metric_Pad0.72x0.64mm_HandSolder
R16, R22: 100R; R_1206_3216Metric_Pad1.30x1.75mm_HandSolder
R20: 10K; R_0402_1005Metric_Pad0.72x0.64mm_HandSolder
R24, R27: 470K; R_0402_1005Metric_Pad0.72x0.64mm_HandSolder
R26: 0R; R_0402_1005Metric_Pad0.72x0.64mm_HandSolder
R41: 160K; R_0402_1005Metric_Pad0.72x0.64mm_HandSolder
U4: LMV611; SOT-23-5

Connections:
+3V3: R29.2; also elsewhere on the board
+12V: Q4.2 (S), R14.1; also elsewhere on the board
/Bluenrg/BRIGHTNESS: U4.3 (-), U4.4; also elsewhere on the board
/Bluenrg/EN_IO: D15.1 (K), J9.2, R13.1, R34.1; also elsewhere on the board
/Bluenrg/LIGHT_BLUE: R33.1; also elsewhere on the board
/Bluenrg/LIGHT_GREEN: R40.2; also elsewhere on the board
/Bluenrg/LIGHT_PWM: R17.1, R23.1; also elsewhere on the board
/Bluenrg/LIGHT_RED: R38.1; also elsewhere on the board
/Bluenrg/LIGHT_WHITE: R36.1; also elsewhere on the board
/Bluenrg/OPENED: R28.1; also elsewhere on the board
/Bluenrg/~LOCK: R18.1; also elsewhere on the board
/InOut/AM_LIGHT_12V_W-: D16.2 (A), J11.1, Q7.3 (D), Q8.3 (D)
/InOut/AM_LIGHT_B_W+: J9.4, J11.2, Q9.3 (D), Q10.3 (D)
/InOut/AM_LIGHT_G: J11.3, Q14.3 (D)
/InOut/AM_LIGHT_POWER: J8.1, Q5.1 (G), Q11.3 (D)
/InOut/AM_LIGHT_R: J11.4, Q13.3 (D)
/InOut/BP_LED_P: D16.1 (K), J9.3
/InOut/BP_NO: D18.1 (K), J9.1, R20.1
/InOut/COIL_N: D10.2 (A), J10.4, Q6.3 (D)
/InOut/COIL_P: C15.1, D10.1 (K), J10.3, R22.2
/InOut/EX_LIGHT_CMD: D11.1 (K), J8.3, Q5.2 (S)
/InOut/POWER_IO_12V: C14.1, Q4.3 (D), Q7.2 (S), Q9.2 (S), Q11.2 (S), R16.1, R24.1, R30.1
GND: C14.2, C15.2, C17.2, C18.2, C19.2, C20.2, D11.2 (A), D15.2 (A), D17.2 (A), D18.2 (A), D20.2 (A), J8.2, J10.1, J12.1, Q3.2 (S), Q6.2 (S), Q8.2 (S), Q10.2 (S), Q12.2 (S), Q13.2 (S), Q14.2 (S), R15.2, R21.2, R25.2, R32.2, R35.2, R37.2, R39.2, U4.2 (V-); also elsewhere on the board
unnamed: C16.2, D12.2 (A), D14.1 (K), R23.2, R25.1, R27.1
unnamed: C16.1, D12.1 (K), D13.2 (A), R24.2, R26.1
unnamed: D13.1 (K), Q7.1 (G), R26.2
unnamed: D14.2 (A), Q8.1 (G), R27.2
unnamed: C17.1, D17.1 (K), J10.2, R28.2, R29.1
unnamed: D19.2 (A), Q10.1 (G), R32.1, R33.2
unnamed: D19.1 (K), Q12.3 (D), R31.2
unnamed: C20.1, D20.1 (K), J12.2, R41.2, U4.1 (+)
unnamed: Q3.3 (D), R19.2
unnamed: Q3.1 (G), R13.2, R15.1
unnamed: Q4.1 (G), R14.2, R19.1
unnamed: Q5.3 (D), R17.2
unnamed: Q6.1 (G), R18.2, R20.2, R21.1
unnamed: Q9.1 (G), Q11.1 (G), R30.2, R31.1
unnamed: Q12.1 (G), R35.1, R36.2
unnamed: Q13.1 (G), R37.1, R38.2
unnamed: Q14.1 (G), R39.1, R40.1
unnamed: R16.2, R22.1
unnamed: C18.1, C19.1, R34.2, R41.1, U4.5 (V+)

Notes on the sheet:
Micro Switch borne NC.
Bouton borne C.
Consommation max pour chaque couleurs (RGBW): 150mA/12V
Led A
Bobine -
Cable vers lumière extérieure (Mini-Light).
Micro Switch borne C.
Cable vers serrures.
Bouton borne NC.
Led K
Consommation max: 400mA/12V
Cable vers capteur de luminosité (carte LightSensor).
Cable vers lumière d'ambiance RGBW.
BP_LED_N
Bobine +
Consommation max (LED bleu): 50mA/12V
Cable vers bouton lumineux.
BP_C

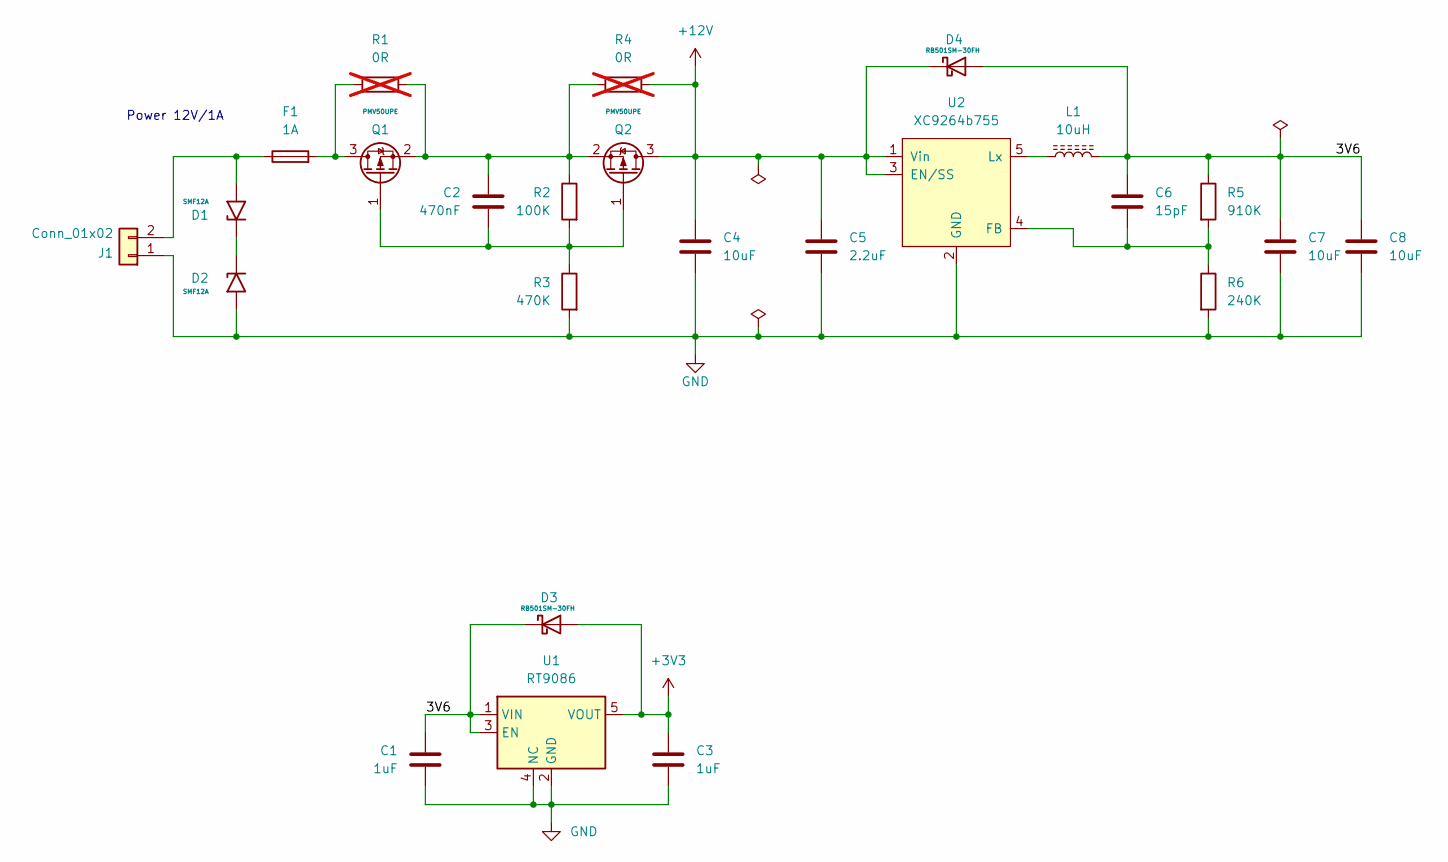
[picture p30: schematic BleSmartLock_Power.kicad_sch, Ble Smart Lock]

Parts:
C1, C3: 1uF; C_0603_1608Metric_Pad1.08x0.95mm_HandSolder
C2: 470nF; C_0603_1608Metric_Pad1.08x0.95mm_HandSolder
C4, C7, C8: 10uF; C_0805_2012Metric_Pad1.18x1.45mm_HandSolder
C5: 2.2uF; C_0603_1608Metric_Pad1.08x0.95mm_HandSolder
C6: 15pF; C_0402_1005Metric_Pad0.74x0.62mm_HandSolder
D1, D2: SMF12A; D_SMF
D3, D4: RB501SM-30FH; D_SOD-523
F1: 1A; L_0603_1608Metric_Pad1.05x0.95mm_HandSolder
J1: Conn_01x02; JST_PH_B2B-PH-K_1x02_P2.00mm_Vertical
L1: 10uH; L_1008_2520Metric_Pad1.43x2.20mm_HandSolder
Q1, Q2: PMV50UPE; SOT-23
R1, R4: 0R; R_0805_2012Metric_Pad1.20x1.40mm_HandSolder; not fitted
R2: 100K; R_0402_1005Metric_Pad0.72x0.64mm_HandSolder
R3: 470K; R_0402_1005Metric_Pad0.72x0.64mm_HandSolder
R5: 910K; R_0402_1005Metric_Pad0.72x0.64mm_HandSolder
R6: 240K; R_0402_1005Metric_Pad0.72x0.64mm_HandSolder
U1: RT9086; SOT-23-5
U2: XC9264b755; SOT-23-5

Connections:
+3V3: C3.1, D3.2 (A), U1.5 (VOUT); also elsewhere on the board
+12V: C4.1, C5.1, D4.1 (K), Q2.3 (D), R4.2, U2.1 (Vin), U2.3 (EN/SS); also elsewhere on the board
/Power/3V6: C1.2, C6.1, C7.1, C8.1, D3.1 (K), D4.2 (A), L1.2, R5.1, U1.1 (VIN), U1.3 (EN)
GND: C1.1, C3.2, C4.2, C5.2, C7.2, C8.2, D2.2 (A2), J1.1, R3.2, R6.2, U1.2 (GND), U1.4 (NC), U2.2 (GND); also elsewhere on the board
unnamed: D1.1 (A1), D2.1 (A1)
unnamed: D1.2 (A2), F1.1, J1.2
unnamed: F1.2, Q1.3 (D), R1.1
unnamed: C2.2, Q1.1 (G), Q2.1 (G), R2.2, R3.1
unnamed: C2.1, Q1.2 (S), Q2.2 (S), R1.2, R2.1, R4.1
unnamed: C6.2, R5.2, R6.1, U2.4 (FB)
unnamed: L1.1, U2.5 (Lx)

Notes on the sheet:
Power 12V/1A

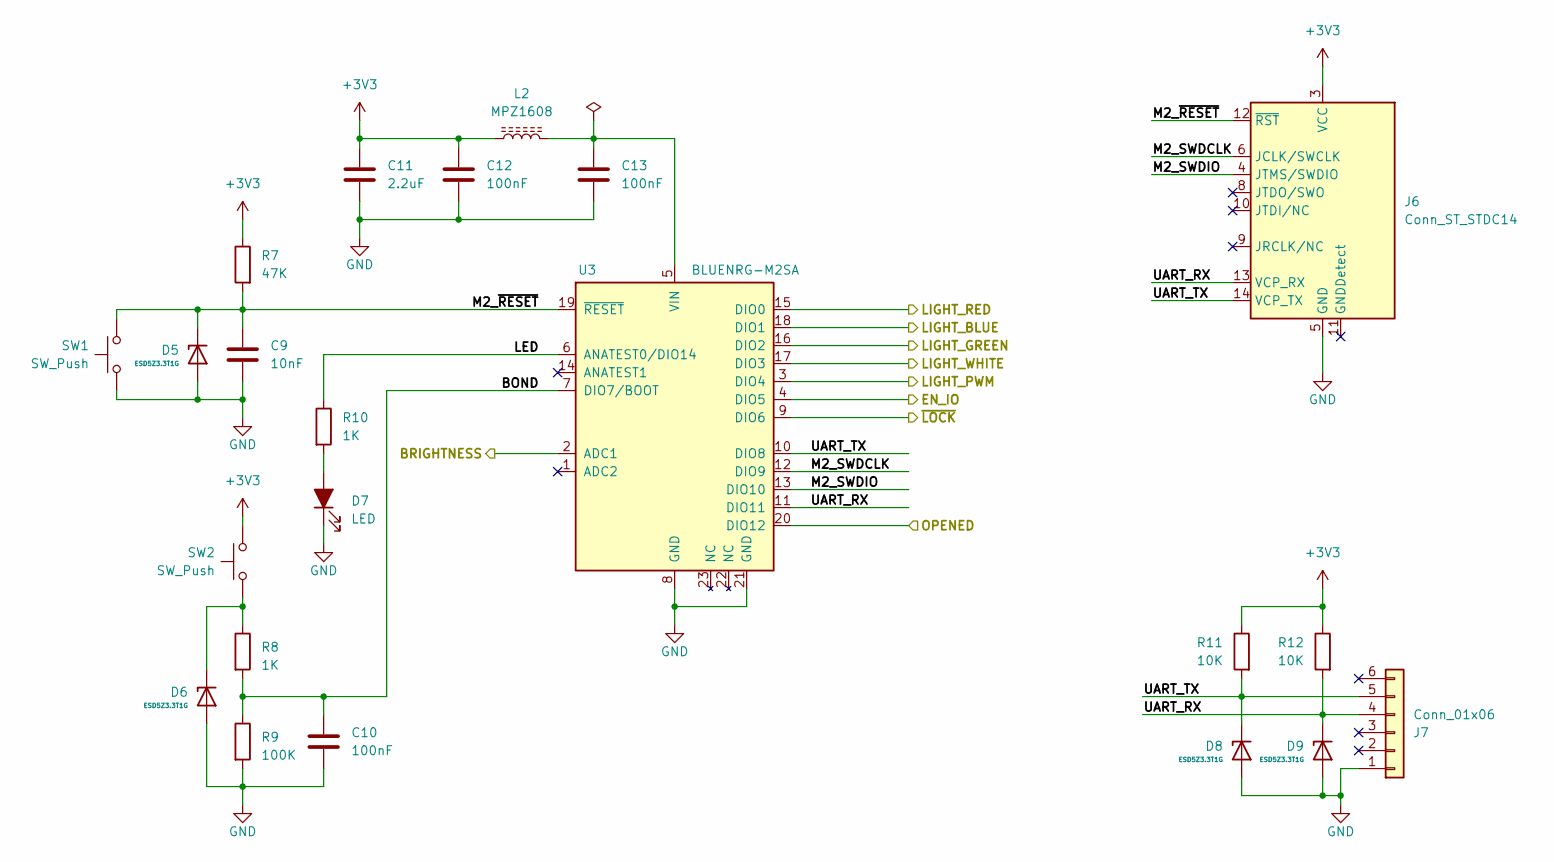
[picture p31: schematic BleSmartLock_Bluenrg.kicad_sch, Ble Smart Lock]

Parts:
C9: 10nF; C_0402_1005Metric_Pad0.74x0.62mm_HandSolder
C10, C12, C13: 100nF; C_0402_1005Metric_Pad0.74x0.62mm_HandSolder
C11: 2.2uF; C_0603_1608Metric_Pad1.08x0.95mm_HandSolder
D5, D6, D8, D9: ESD5Z3.3T1G; D_SOD-523
D7: LED; LED_0603_1608Metric_Pad1.05x0.95mm_HandSolder
J6: Conn_ST_STDC14; PinHeader_2x07_P1.27mm_Vertical_SMD
J7: Conn_01x06; PinHeader_1x06_P2.54mm_Vertical
L2: MPZ1608; L_0603_1608Metric_Pad1.05x0.95mm_HandSolder
R7: 47K; R_0402_1005Metric_Pad0.72x0.64mm_HandSolder
R8, R10: 1K; R_0402_1005Metric_Pad0.72x0.64mm_HandSolder
R9: 100K; R_0402_1005Metric_Pad0.72x0.64mm_HandSolder
R11, R12: 10K; R_0402_1005Metric_Pad0.72x0.64mm_HandSolder
SW1, SW2: SW_Push; SW_SPST_PTS645
U3: BLUENRG-M2SA

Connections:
+3V3: C11.1, C12.1, J6.3 (VCC), L2.1, R7.1, R11.1, R12.1, SW2.1; also elsewhere on the board
/Bluenrg/BOND: C10.1, R8.2, R9.1, U3.7 (DIO7/BOOT)
/Bluenrg/BRIGHTNESS: U3.2 (ADC1); also elsewhere on the board
/Bluenrg/EN_IO: U3.4 (DIO5); also elsewhere on the board
/Bluenrg/LED: R10.1, U3.6 (ANATEST0/DIO14)
/Bluenrg/LIGHT_BLUE: U3.18 (DIO1); also elsewhere on the board
/Bluenrg/LIGHT_GREEN: U3.16 (DIO2); also elsewhere on the board
/Bluenrg/LIGHT_PWM: U3.3 (DIO4); also elsewhere on the board
/Bluenrg/LIGHT_RED: U3.15 (DIO0); also elsewhere on the board
/Bluenrg/LIGHT_WHITE: U3.17 (DIO3); also elsewhere on the board
/Bluenrg/M2_SWDCLK: J6.6 (JCLK/SWCLK), U3.12 (DIO9)
/Bluenrg/M2_SWDIO: J6.4 (JTMS/SWDIO), U3.13 (DIO10)
/Bluenrg/M2_~RESET: C9.1, D5.1 (K), J6.12 (~RST), R7.2, SW1.1, U3.19 (~RESET)
/Bluenrg/OPENED: U3.20 (DIO12); also elsewhere on the board
/Bluenrg/UART_RX: D9.1 (K), J6.13 (VCP_RX), J7.4, R12.2, U3.11 (DIO11)
/Bluenrg/UART_TX: D8.1 (K), J6.14 (VCP_TX), J7.5, R11.2, U3.10 (DIO8)
/Bluenrg/~LOCK: U3.9 (DIO6); also elsewhere on the board
GND: C9.2, C10.2, C11.2, C12.2, C13.2, D5.2 (A), D6.2 (A), D7.1 (K), D8.2 (A), D9.2 (A), J6.5 (GND), J6.7 (GND), J7.1, R9.2, SW1.2, U3.8 (GND), U3.21 (GND); also elsewhere on the board
unnamed: D6.1 (K), R8.1, SW2.2
unnamed: D7.2 (A), R10.2
unnamed: C13.1, L2.2, U3.5 (VIN)

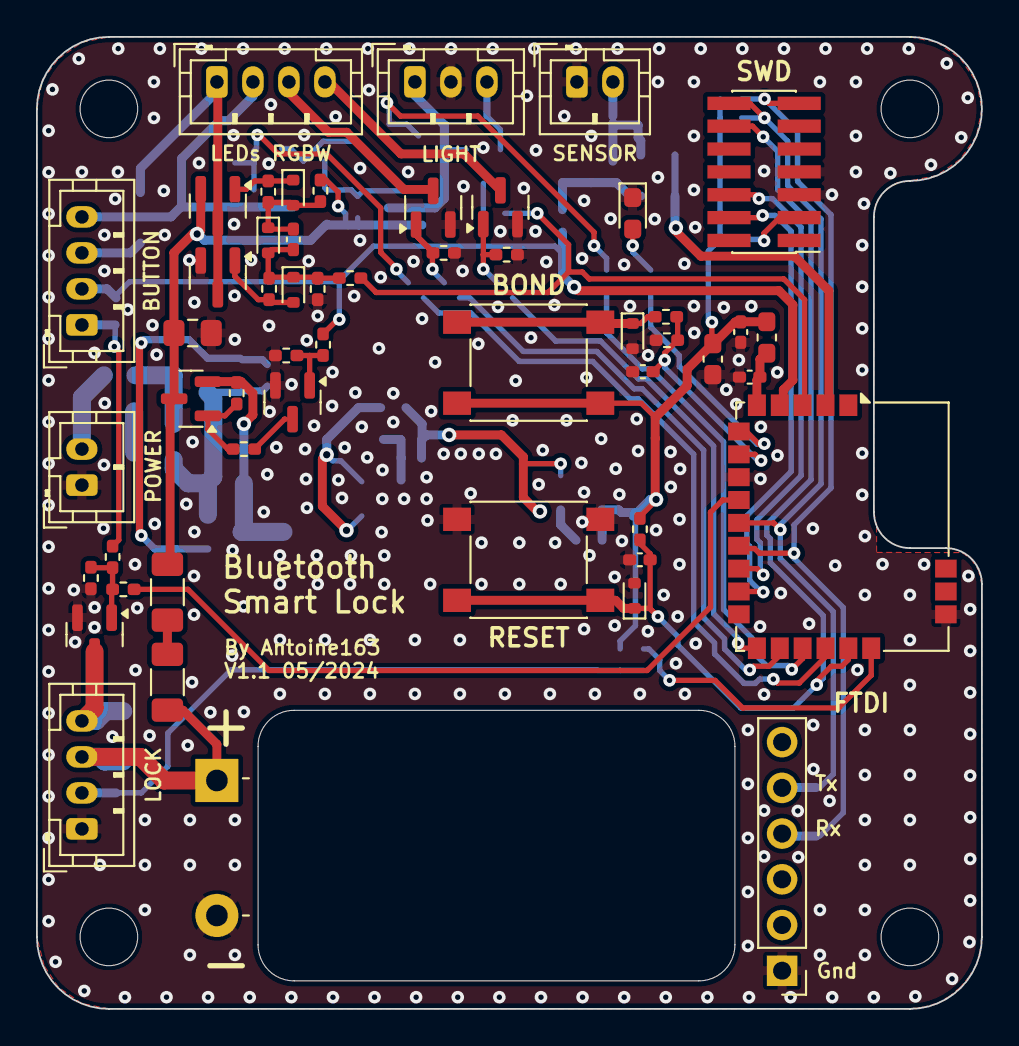
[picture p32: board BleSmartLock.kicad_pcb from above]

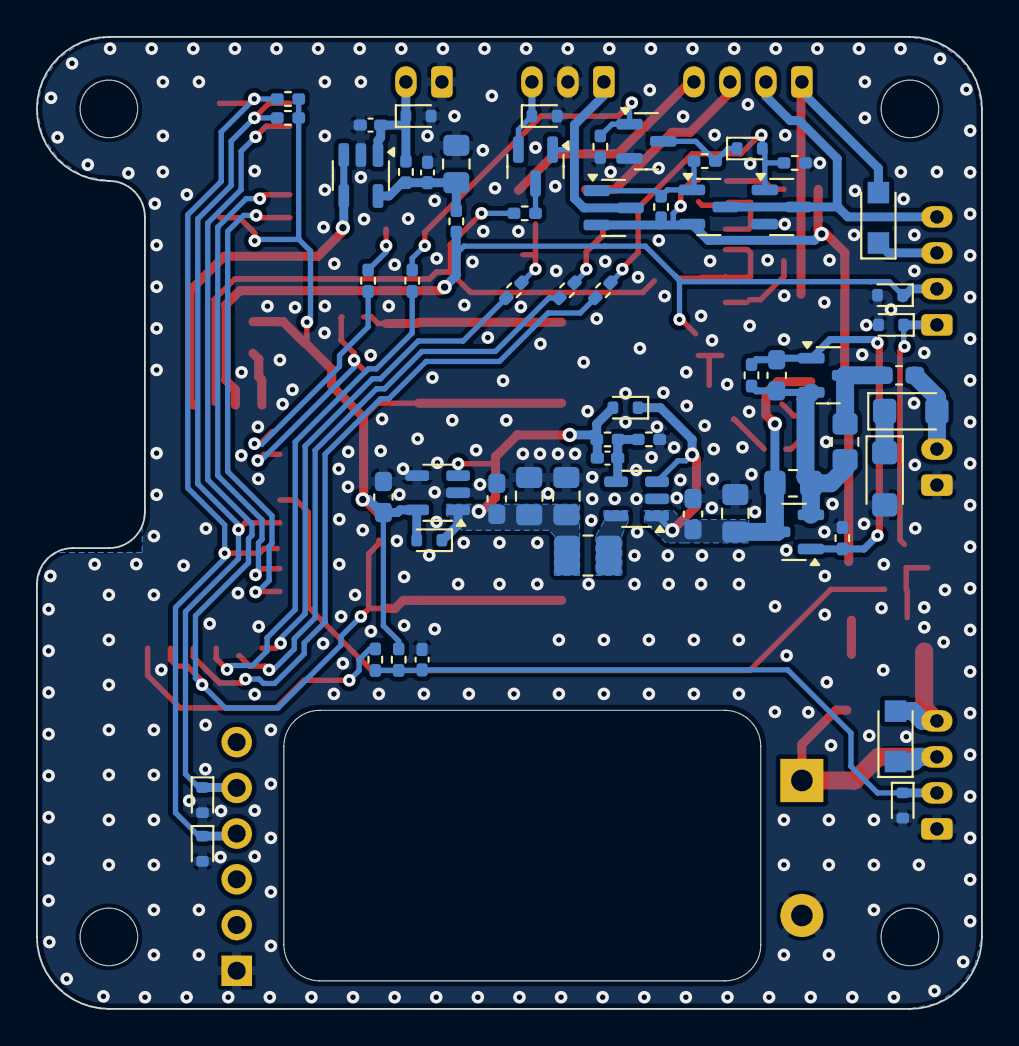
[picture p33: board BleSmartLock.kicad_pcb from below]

Board: 2 copper layers, 52.5 x 54.0 mm, 116 parts (60 on the bottom side), 60 nets.

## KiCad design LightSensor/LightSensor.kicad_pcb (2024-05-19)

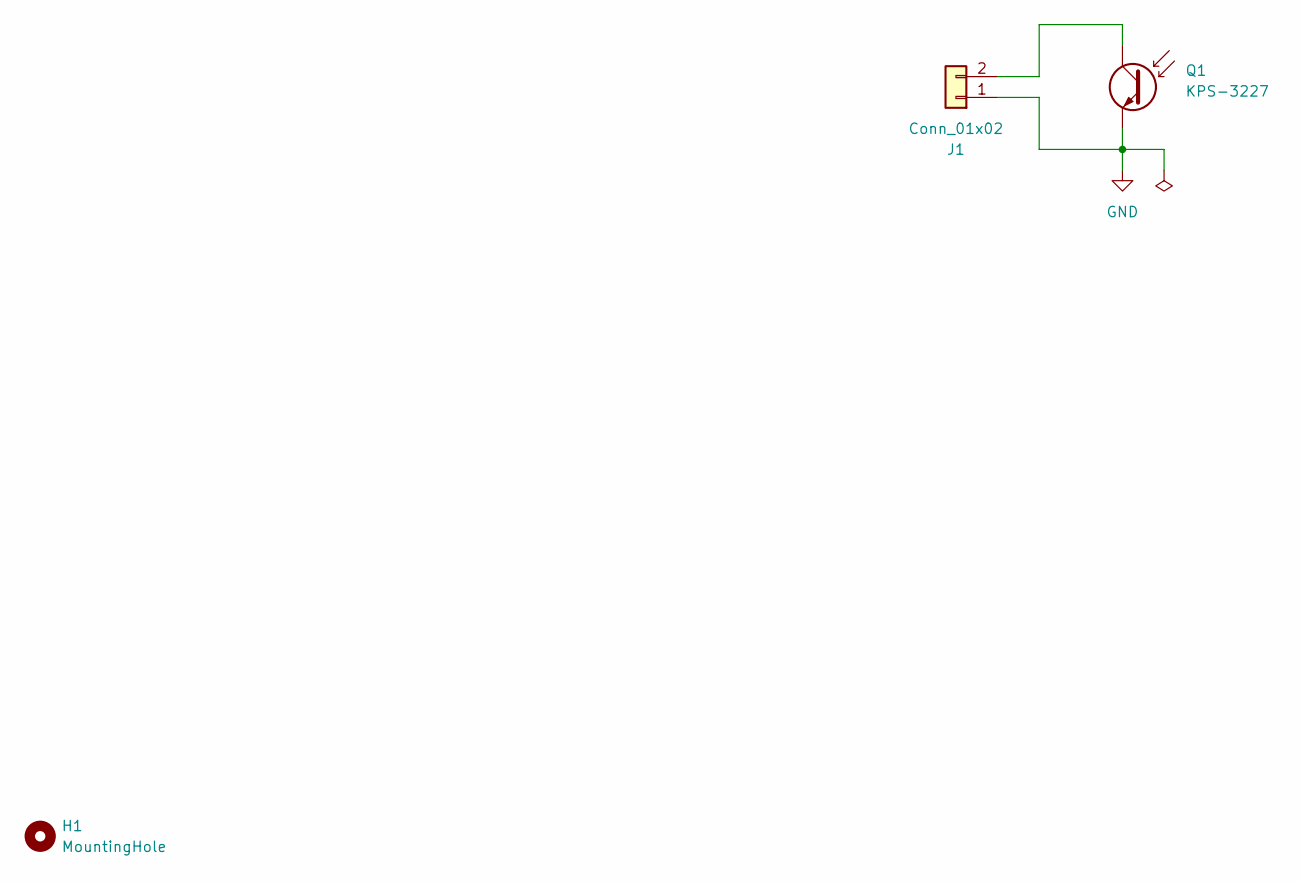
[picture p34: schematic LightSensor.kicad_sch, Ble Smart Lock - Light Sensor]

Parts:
H1: MountingHole; MountingHole_3.2mm_M3
J1: Conn_01x02; JST_PH_B2B-PH-K_1x02_P2.00mm_Vertical
Q1: KPS-3227; Kingbright_KPS-3227

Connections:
GND: J1.1, Q1.2, Q1.4
unnamed: J1.2, Q1.1, Q1.3

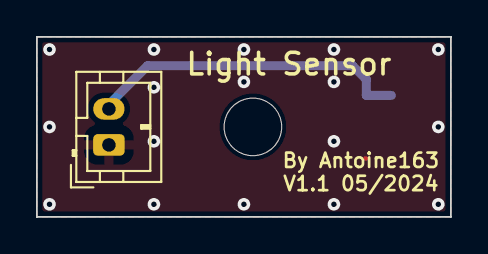
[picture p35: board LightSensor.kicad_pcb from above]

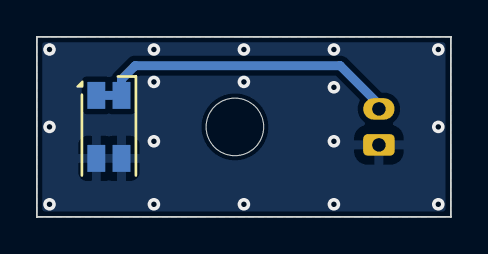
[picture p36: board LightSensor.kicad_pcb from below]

Board: 2 copper layers, 23.0 x 10.0 mm, 3 parts (2 on the bottom side), 2 nets.

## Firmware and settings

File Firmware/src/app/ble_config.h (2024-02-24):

/***
 * The MIT License (MIT)
 *
 * Copyright (c) 2023 antoine163
 * 
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
 * THE SOFTWARE IS PROVIDED "AS IS", WITHOUT WARRANTY OF ANY KIND, EXPRESS OR
 * IMPLIED, INCLUDING BUT NOT LIMITED TO THE WARRANTIES OF MERCHANTABILITY,
 * FITNESS FOR A PARTICULAR PURPOSE AND NONINFRINGEMENT. IN NO EVENT SHALL THE
 * AUTHORS OR COPYRIGHT HOLDERS BE LIABLE FOR ANY CLAIM, DAMAGES OR OTHER
 * LIABILITY, WHETHER IN AN ACTION OF CONTRACT, TORT OR OTHERWISE, ARISING FROM,
 * OUT OF OR IN CONNECTION WITH THE SOFTWARE OR THE USE OR OTHER DEALINGS IN THE
 * SOFTWARE.
 */

/**
 * @file ble_config.h
 * @author antoine163
 * @date 15.07.2023
 * @brief This file is recovered and adjusted from examples of ST.
 * It contains all the information needed to init the BlueNRG-1 stack.
 * These constants and variables are used from the BlueNRG-1 stack to reserve
 * RAM and FLASH according the application requests.
 */

#ifndef BLE_CONFIG_H
#define BLE_CONFIG_H

#include "bluenrg1_stack.h"
#include "stack_user_cfg.h"
#include "OTA_btl.h"

/* Default number of link */
#define MIN_NUM_LINK            1
/* Default number of GAP and GATT services */
#define DEFAULT_NUM_GATT_SERVICES   2
/* Default number of GAP and GATT attributes */
#define DEFAULT_NUM_GATT_ATTRIBUTES 9

/* Enable/disable Data length extension Max supported ATT_MTU size based on OTA client & server Max ATT_MTU sizes capabilities */
#if (CONTROLLER_DATA_LENGTH_EXTENSION_ENABLED == 1) && (OTA_EXTENDED_PACKET_LEN == 1)
    #define OTA_MAX_ATT_MTU_SIZE    (OTA_ATT_MTU_SIZE) //(220) /* OTA Client & Server supported ATT_MTU */
#else /* BlueNRG-1 device: no data length extension support */
    #define OTA_MAX_ATT_MTU_SIZE    (DEFAULT_ATT_MTU)          /* DEFAULT_ATT_MTU size = 23 bytes */
#endif

#if defined (ST_OTA_LOWER_APPLICATION) || defined (ST_OTA_HIGHER_APPLICATION)
    /* Number of services requests from the bl unlocker */
    #define NUM_APP_GATT_SERVICES (1 + 1) /* 1 bl unlocker service + 1 OTA service */
    /* Number of attributes requests from the bl unlocker */
    #define NUM_APP_GATT_ATTRIBUTES (5 + 9) /* 5 attributes x BLE bl unlocker service characteristics + 9 for OTA Service characteristics */
    /**
     * Set the number of 16-bytes units used on an OTA FW data packet for matching OTA client MAX ATT_MTU
     */
    #define OTA_16_BYTES_BLOCKS_NUMBER ((OTA_MAX_ATT_MTU_SIZE-4)/16)   /* 4 bytes for OTA sequence numbers + needs ack + checksum bytes */
    /* OTA characteristics maximum lenght */
    #define OTA_MAX_ATT_SIZE (4 + OTA_16_BYTES_BLOCKS_NUMBER * 16)
#else /* NO OTA Service is required */
    /* Number of services requests from the bl unlocker */
    #define NUM_APP_GATT_SERVICES 2  /* 1 bl unlocker service */
    /* Number of attributes requests from the bl unlocker demo */
    #define NUM_APP_GATT_ATTRIBUTES 16 /* ? attributes x BLE bl unlocker service characteristics */
    /* OTA characteristics maximum lenght */
    #define OTA_MAX_ATT_SIZE (0)
#endif

#define MAX_CHAR_LEN(a,b) ((a) > (b) )? (a) : (b)

/* Application characteristics maximum lenght */
#define _MAX_ATT_SIZE	(6)

/* Set supported max value for attribute size: it is the biggest attribute size enabled by the application. */
#define APP_MAX_ATT_SIZE	  MAX_CHAR_LEN(OTA_MAX_ATT_SIZE,  _MAX_ATT_SIZE)

/* Number of links needed for bl unlocker.
 * Only 1 the default
 */
#define NUM_LINKS               (MIN_NUM_LINK)

/* Number of GATT attributes needed for the bl unlocker. */
#define NUM_GATT_ATTRIBUTES     (DEFAULT_NUM_GATT_ATTRIBUTES + NUM_APP_GATT_ATTRIBUTES)

/* Number of GATT services needed for the bl unlocker. */
#define NUM_GATT_SERVICES       (DEFAULT_NUM_GATT_SERVICES + NUM_APP_GATT_SERVICES)

/* Array size for the attribute value for OTA service */
#if defined (ST_OTA_LOWER_APPLICATION) || defined (ST_OTA_HIGHER_APPLICATION)
/* OTA service: 4 characteristics (1 notify property): 99 bytes +
   Image Content characteristic length = 4  + (OTA_16_BYTES_BLOCKS_NUMBER * 16); 4 for sequence number, checksum and needs acks bytes */
#define OTA_ATT_VALUE_ARRAY_SIZE (99 + (4 + (OTA_16_BYTES_BLOCKS_NUMBER * 16)))
#else
#define OTA_ATT_VALUE_ARRAY_SIZE (0)       /* No OTA service is used */
#endif

/* Array size for the attribute value */
#define ATT_VALUE_ARRAY_SIZE    (44 + 120  + OTA_ATT_VALUE_ARRAY_SIZE) //(GATT + GAP) = 44 + Lock (Unlock (1+19+2=22) + Status ((1+19+2=22)) characteristics))  Services

/* Flash security database size */
#define FLASH_SEC_DB_SIZE       (0x400)

/* Flash server database size */
#define FLASH_SERVER_DB_SIZE    (0x400)

/* Set supported max value for ATT_MTU enabled by the application */
#if (CONTROLLER_DATA_LENGTH_EXTENSION_ENABLED == 1) && (OTA_EXTENDED_PACKET_LEN == 1)
#define MAX_ATT_MTU             (OTA_MAX_ATT_MTU_SIZE)
#else
#define MAX_ATT_MTU             (DEFAULT_ATT_MTU)
#endif

/* Set supported max value for attribute size: it is the biggest attribute size enabled by the application */
#define MAX_ATT_SIZE            (APP_MAX_ATT_SIZE)

/* Set the minumum number of prepare write requests needed for a long write procedure for a characteristic with len > 20bytes:
 *
 * It returns 0 for characteristics with len <= 20bytes
 *
 * NOTE: If prepare write requests are used for a characteristic (reliable write on multiple characteristics), then
 * this value should be set to the number of prepare write needed by the application.
 *
 *  [New parameter added on BLE stack v2.x]
*/
#define PREPARE_WRITE_LIST_SIZE PREP_WRITE_X_ATT(MAX_ATT_SIZE)

/* Additional number of memory blocks  to be added to the minimum  */
#define OPT_MBLOCKS		(6) /* 6:  for reaching the max throughput: ~220kbps (same as BLE stack 1.x) */

/* Set the number of memory block for packet allocation */
#define MBLOCKS_COUNT           (MBLOCKS_CALC(PREPARE_WRITE_LIST_SIZE, MAX_ATT_MTU, NUM_LINKS) + OPT_MBLOCKS)

/* RAM reserved to manage all the data stack according the number of links,
 * number of services, number of attributes and attribute value length
 */
NO_INIT(uint32_t dyn_alloc_a[TOTAL_BUFFER_SIZE(NUM_LINKS,NUM_GATT_ATTRIBUTES,NUM_GATT_SERVICES,ATT_VALUE_ARRAY_SIZE,MBLOCKS_COUNT,CONTROLLER_DATA_LENGTH_EXTENSION_ENABLED)>>2]);


/* FLASH reserved to store all the security database information and
 * and the server database information
 */
NO_INIT_SECTION(uint32_t stacklib_flash_data[TOTAL_FLASH_BUFFER_SIZE(FLASH_SEC_DB_SIZE, FLASH_SERVER_DB_SIZE)>>2], ".noinit.stacklib_flash_data");

/* FLASH reserved to store: security root keys, static random address, public address */
NO_INIT_SECTION(uint8_t stacklib_stored_device_id_data[56], ".noinit.stacklib_stored_device_id_data");

/* Maximum duration of the connection event */
#define MAX_CONN_EVENT_LENGTH 0xFFFFFFFF

/* Sleep clock accuracy */
#if (LS_SOURCE == LS_SOURCE_INTERNAL_RO)
    /* Sleep clock accuracy in Slave mode */
    #define SLAVE_SLEEP_CLOCK_ACCURACY 500
    /* Sleep clock accuracy in Master mode */
    #define MASTER_SLEEP_CLOCK_ACCURACY MASTER_SCA_500ppm
#else
    /* Sleep clock accuracy in Slave mode */
    #define SLAVE_SLEEP_CLOCK_ACCURACY 100

    /* Sleep clock accuracy in Master mode */
    #define MASTER_SLEEP_CLOCK_ACCURACY MASTER_SCA_100ppm
#endif

/* Low Speed Oscillator source */
#if (LS_SOURCE == LS_SOURCE_INTERNAL_RO)
    #define LOW_SPEED_SOURCE  1 // Internal RO
#else
    #define LOW_SPEED_SOURCE  0 // External 32 KHz
#endif

/* High Speed start up time */
#define HS_STARTUP_TIME 328 // 800 us

/* Radio Config Hot Table */
extern uint8_t hot_table_radio_config[];

/* Low level hardware configuration data for the device */
#define CONFIG_TABLE            \
{                               \
        (uint32_t*)hot_table_radio_config,          \
        MAX_CONN_EVENT_LENGTH,        \
        SLAVE_SLEEP_CLOCK_ACCURACY,   \
        MASTER_SLEEP_CLOCK_ACCURACY,  \
        LOW_SPEED_SOURCE,             \
        HS_STARTUP_TIME               \
}

/* This structure contains memory and low level hardware configuration data for the device */
const BlueNRG_Stack_Initialization_t BlueNRG_Stack_Init_params = {
    (uint8_t*)stacklib_flash_data,
    FLASH_SEC_DB_SIZE,
    FLASH_SERVER_DB_SIZE,
    (uint8_t*)stacklib_stored_device_id_data,
    (uint8_t*)dyn_alloc_a,
    TOTAL_BUFFER_SIZE(NUM_LINKS,NUM_GATT_ATTRIBUTES,NUM_GATT_SERVICES,ATT_VALUE_ARRAY_SIZE,MBLOCKS_COUNT,CONTROLLER_DATA_LENGTH_EXTENSION_ENABLED),
    NUM_GATT_ATTRIBUTES,
    NUM_GATT_SERVICES,
    ATT_VALUE_ARRAY_SIZE,
    NUM_LINKS,
    0, /* reserved for future use */
    PREPARE_WRITE_LIST_SIZE,
    MBLOCKS_COUNT,
    MAX_ATT_MTU,
    CONFIG_TABLE,
};

#endif // BLE_CONFIG_H

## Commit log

2024-01-27 readme de description du project
2024-02-18 Ajout des fichiers kicad.
    [BleSmartLock.kicad_pcb, BleSmartLock.kicad_sch, BleSmartLock_Bluenrg.kicad_sch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]
2024-02-24 [firm] Ajout des premier fichiers compilable
    [bluenrg-2.cfg, gdb_target.cfg, gdbinit_debug.cfg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]
2024-03-16 Re-organisation des dossiers (déplacement du kicad BleSmartLock et du firmware)
    [BleSmartLock.kicad_pcb, BleSmartLock.kicad_sch, BleSmartLock_Bluenrg.kicad_sch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]
2024-03-16 ajout carte LightSensor
    [LightSensor.kicad_pcb, LightSensor.kicad_sch]
2024-03-30 Ajout carte BleSmartLock
    [BleSmartLock.kicad_pcb, BleSmartLock.kicad_sch, BleSmartLock_Bluenrg.kicad_sch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]
2024-03-30 Ajout fichier de production et bom interactive
    [BleSmartLock.kicad_pcb, BleSmartLock_Power.kicad_sch]
2024-03-31 Déplace les images dans le dossier images
2024-03-31 Ajout fichier de production de la carte LightSensor
    [LightSensor.kicad_pcb, LightSensor.kicad_sch]
2024-04-01 Ajustement pour prendre en compte les dernières modifications hardware.
2024-04-01 [firm] Remise en place de l'uart
2024-04-04 [firm] Mise en place rapide de la tache ble
2024-04-06 [firm] Driver pwm
2024-04-09 [firm] amelioration du pilotage des leds
2024-04-11 [firm] Implementation de taskLightSetColor() et simplification temporaire de la tache light
2024-04-13 Implementation de boardGetBrightness() / ADC
2024-04-13 Ajout des fonctions 'board' pour verrouiller/déverrouiller et ouvrier la serrure
2024-04-19 Envoie un message à la tache App suit à l'appuis sur le bouton Bond
2024-04-28 Configuration de ta stack BLE avec 1 service et 5 caractéristiques
2024-05-01 Renommage des msg en event et init des taches
2024-05-01 Implementation des différents état de la serrure
2024-05-01 Prise en comte du seuil de luminosité pour allumer ou pas la lumière extérieur.
2024-05-01 Ajout des couleurs et un manager de couleur dans la tache App
2024-05-03 Implement la tache light pour gérer les animations lumineuse
2024-05-05 Débogage et améliore les animations lumineuse
2024-05-05 Correction flache lumineux au changement de couleur
2024-05-06 Petite correction de bug au démarrage de clignotement
2024-05-06 Aller plus proche du dc 0 dans boardSetLightDc
2024-05-06 Allume la lumière externe suite à l'ouverture via la clef même sur le ble est déconnecter.
2024-05-06 Pilotage de EN_IO en fonction du besoin
2024-05-06 Ne pas fair de pub BLE si la porte est ouvert au boot
2024-05-06 Petit mise à jour du readme + comportement led rouge
2024-05-06 Éteint les lumières d'ambience si plus d’activité + reset sui a une erreur.
2024-05-06 Correction de bug sur les transitoires de même couleur.
2024-05-09 Gross revue de la tache BLE permettent l’appairage (il reste encore quelque zone brouillon)
2024-05-18 Suppression des devices liers suit appuis long sur le bouton bond. implementation de taskBleUpdateAtt. Gestion de la liste blanche.
2024-05-19 Mise a jour pcb en v1.1 et readme
    [BleSmartLock.kicad_pcb, BleSmartLock.kicad_sch, BleSmartLock_Bluenrg.kicad_sch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]
2024-05-19 Numéro de version depuis le dernier hash git
2024-05-19 Renommage 'action' en 'flag' dans la tache ble et mise à jour des de la luminosité suit demande ble
2024-05-19 Mise a jour de l'attribue BLE en fonction de l’état de la port.
2024-05-20 Réorganise le scrip de lien pour à jouter une section NVM2 et nettoyer les sections OTA inutile ici?
2024-05-20 Écriture/lecture des données de l'app depuis la flash
2024-05-20 Utiliser des flags dans la tach app plu que des actions. + Ammonisation
2024-05-25 PIN depuis la flash
2024-05-25 Ajout boardDgb + squelette de la tache term
2024-05-25 fixbug dans boardDgb
2024-05-26 fixbug in uart
2024-06-01 Ajour la commande top pour afficher le status des taches
2024-06-01 cmd pin
2024-06-08 Ajout function uart_waitWrite
2024-06-08 Ajuste la taille des taches
2024-06-09 Réveille à l'ouverture de la porte
2024-06-09 Ajout des régles cgdb et load
    [bluenrg-2.cfg, gdb_target.cfg]
2024-08-08 Fix : Correction du comportement du paramètre 'verbose' dans la fonction _taskTermCmdVerbose() pour qu'il désactive effectivement l'affichage des informations détaillées lorsqu'on spécifie 'disable' 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
2024-08-08 Corrigé une erreur d'orthographe dans la fonction taskAppOpenDoor() : foor -> Door
2024-10-12 Separation du hardware du depo principale
    [BleSmartLock.kicad_pcb, BleSmartLock.kicad_sch, BleSmartLock_Bluenrg.kicad_sch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]
